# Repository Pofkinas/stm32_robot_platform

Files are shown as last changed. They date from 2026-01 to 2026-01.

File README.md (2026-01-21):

# STM32 Robot Platform

Modular robot platform for experimenting with basic robotics. Built around STM32F411RE (main controller) and ESP32 (encoder bridge + web interface).

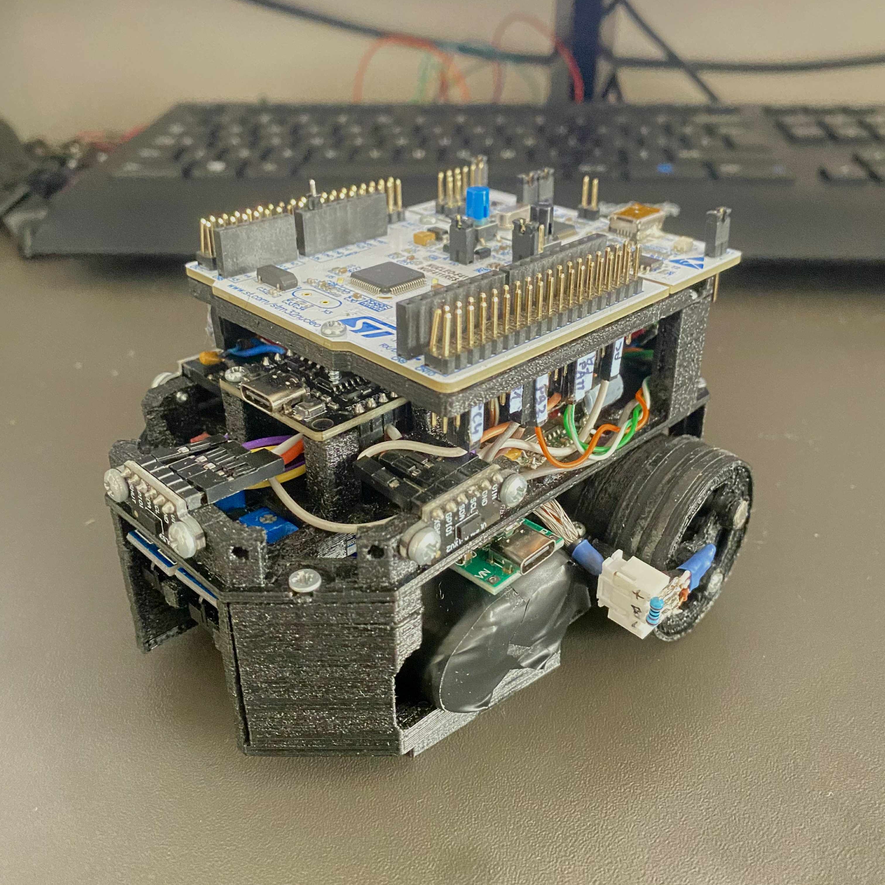
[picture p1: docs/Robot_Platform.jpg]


## Hardware

The platform uses 3D-printed chassis designed for modularity and easy prototyping. It is possible to configure sensor layer by suppressing/unsuppressing features. All parts are available as Fusion 360 files (`.f3z`) in the `hardware/` directory.

**Components:**

- STM32F411RE Nucleo board
- ESP32 DevKit
- TB6612FNG motor driver
- 2× 130 DC 3-6 V motors with custom 36:1 planetary gearboxes
- 3× VL53L0X time-of-flight sensors
- 2× DRV5032FCDBZR hall effect sensors for wheel encoders (see notes below)
- 2× TCRT5000 tracking sensors (not currently implemented)
- User button on PC0 (not currently implemented)
- MINI360 DC-DC step down buck converter (logic circuit)
- XL4015 DC-DC step down buck converter (power circuit)
- 18650 2S 15C Li-Ion battery pack

**Pinout:**

| **STM32 Pin** | **Function** |
|---|---|
| PA9, PA10 | UART TX/RX (ESP32 communication) |
| PB0, PB1 | Motor PWM (right, left) |
| PA4, PB2 | Motor A direction (IN1, IN2) |
| PA11, PA12 | Motor B direction (IN2, IN1) |
| PC1, PA6 | TCRT sensors (right, left) |
| PB8, PB9 | I2C1 SCL/SDA (VL53L0X) |
| PC4, PC5, PC2 | VL53L0X XSHUT (left, center, right) |
| PC0 | User button (reserved for future use) |

| **ESP32 Pin** | **Function** |
|---|---|
| D16, D17 | UART2 TX/RX (STM32 communication) |
| D4, D13 | Encoder interrupts (left, right) |

## Architecture

The firmware is structured around a mission-based task scheduler running as the main thread, periodically updating available tasks. Each mission consists of multiple tasks, with each task containing a sequence of actions that can be combined to create autonomous behaviors.

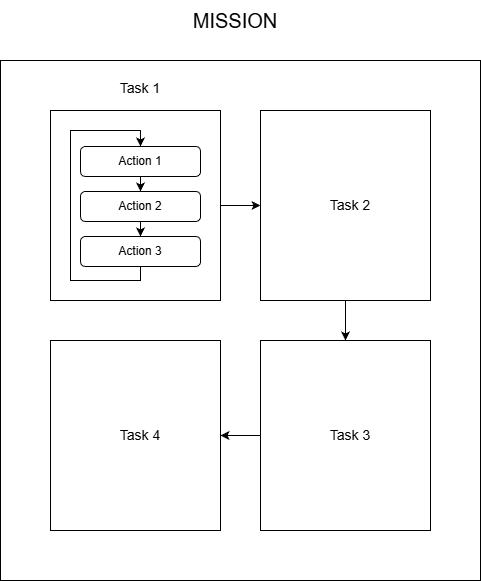
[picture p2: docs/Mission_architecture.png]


**Mission Architecture Flow:**
- Missions are queued in the scheduler and executed sequentially
- Each mission contains one or more tasks
- Tasks are broken down into actions (DriveDistance, Measure, WallFollow) that are serviced periodically
- Actions report completion status, allowing the scheduler to advance to the next step
- Failed actions trigger error handling and mission cancellation

**Available Actions:**
- `DriveDistance` — drives to set heading (degrees) for a specified distance (mm) at set speed (mm/s) using encoder feedback and odometry
- `Measure` — reads selected VL53L0X sensors
- `WallFollow` — follows a wall (left/right/center) at set speed (%) maintaining set offset distance using PID control

Missions are defined as semicolon-delimited strings sent via CLI or web interface. The mission scheduler executes actions sequentially.

**Communication Protocol:**

A custom binary protocol over UART between STM32 and ESP32 uses the following message structure:

```
[CMD_BYTE:1][ARG_COUNT:1][ARGS:n][\n]
```

- **CMD_BYTE**: 8-bit value containing command ID (7 bits) and direction bit (1 bit)
  - Bit 0: Direction (0=request, 1=response)
  - Bits 1-7: Command ID
- **ARG_COUNT**: Number of bytes in the arguments section
- **ARGS**: Raw argument data string (optional)
- **\n**: Message delimiter

## Control Panel Webpage

The web interface provides button-based command formation with two modes: instant send (commands execute immediately with field values) or manual construction via the custom command field (command buttons prefill this field). Mission builder allows creating multi-action sequences by adding tasks like "Measure" and "Wall Follow" with configurable parameters. All sent commands and debug messages from the STM32 are displayed in the real-time log panel. See `docs/Control_Panel.png`

## Software Architecture

```
stm32/                   # STM32 firmware
├── Application/
│   ├── Action/          # Action implementations
│   ├── Config/          # Hardware abstraction configs
│   ├── main.c
│   ├── mission_app.c    # Mission scheduler
│   ├── kinematics_app.c # Motor control, odometry
│   └── esp_comm_app.c   # ESP32 communication handler
├── Framework/           # PDF framework (submodule)
└── ThirdParty/          # STM32 HAL, FreeRTOS

esp32/                   # ESP32 firmware (PlatformIO)
├── src/                 # Main source
│   ├── main.cpp
│   ├── encoder.cpp      # Hall sensor interrupt handling
│   └── esp_protocol.cpp # UART protocol implementation
├── lib/                 # Web server, WiFi, logging
└── data/                # Web interface files (served via LittleFS)
```

**Dependencies:**
- STM32 firmware uses PDF (Platform Driver Framework) as a hardware abstraction layer, included as a git submodule from [github.com/Pofkinas/pdf](https://github.com/Pofkinas/pdf)
- ESP32 uses file system (LittleFS) to house web page, included as library dependency from [github.com/joltwallet/esp_littlefs](https://github.com/joltwallet/esp_littlefs.git#v1.20.3)

## Odometry & Kinematics

The `kinematics_app` tracks robot position and heading using differential drive equations. Encoder data from ESP32 (wheel RPM) is converted to linear and angular velocity, then integrated to estimate:
- X/Y position (mm) in global frame
- Heading angle (degrees)
- Velocity (mm/s)

## CLI Commands

The STM32 exposes a command-line interface via UART. Commands can be sent from a serial terminal or via the web interface. Alternatively, enable the CLI by defining `ENABLE_CLI` in `platform_config.h` and setting `DEBUG_UART` to `UART2` (ST-Link). Note that enabling CLI on the debug UART will disable debug message forwarding to the Robot Control Panel webpage.

See `stm32/Application/custom_cli_lut.c` for complete command list and syntax.

## VL53L0X Time-of-Flight Sensors

The robot uses three VL53L0X sensors operating in a custom high-speed, high-accuracy profile. On boot, the firmware performs automatic calibration (offset and crosstalk) to compensate for environmental conditions.

**Calibration Process:**
- Place robot in similar operating conditions with white calibration targets perpendicular to sensors at 100 mm distance
- Power on and wait for calibration to complete (~15 seconds)
- View calibration values printed in Robot Platform Control Panel

To disable the calibration process, set `.has_calib_data` to `true` in `stm32/Application/Config/vl53l0xv2_config.c` for each sensor and prefill calibration values from a previous calibration run (printed via debug UART).

## Build & Flash

When cloning/forking repo, init PDF submodules via:
```bash
git submodule update --init --recursive
```

**STM32:**
- Import `stm32/` as "Existing project" into Workspace in STM32CubeIDE
- Build and flash via ST-Link

**ESP32:**
- Install PlatformIO
- Navigate to `esp32/` and run `pio run -t upload`
- Upload filesystem: `pio run -t uploadfs`

**Web Interface:**
- Connect ESP32 to WiFi network (enter credentials in `esp32/include/config.h`)
- Using a serial console (baudrate 115200), reboot the ESP32 and watch logs for the hosted IP address
- Navigate to the ESP32's IP address in a browser

## PID Wall-Follow Tuning

The wall-follow action uses a PID controller to maintain a target distance from walls. Motor speed imbalance is partly offset by proportional value `MOTOR_x_SPEED_OFFSET` in `stm32\Application\Config\motor_config.h`.

**Quick tuning procedure:**
1. Start with Ki = 0, Kd = 0
2. Increase Kp until the robot oscillates, then reduce by 30-50%
3. Add Kd to dampen oscillation and reduce overshoot
4. Add minimal Ki to eliminate steady-state drift

## Known Issues

**Hall sensor choice:** The current hall sensors are practically unusable in encoder applications because of their low sampling rate of only 5 Hz. Consider upgrading to at least 1 kHz sampling rate **omnipolar non-latching** sensors. It is possible to embed magnets while printing in `Planet carrier middle`, removing the need for external encoder arm and fitting everything in a smaller footprint. Though for this case use sensors with at least 5 kHz (~12000 rpm / 6 (first stage gear ratio 6:1) × 3 magnets / 60) sampling rate.

**Wall-follow task:** Current implementation uses sensor data to calculate error for the PID controller, which directly adjusts motor speed (%). A better approach would be to control heading via the kinematics app. This primitive solution was a workaround for unreliable encoder sensors.

**ESP protocol:** Current implementation is overly complicated and confusing. Consider using dedicated bytes for actual commands instead of strings with byte count, plus adding error checking mechanisms (CRC, checksums).

**Motor RPM control:** Due to unusable encoders, motor RPM control and every component based on it (`motor_api` RPM control, `kinematics_app`, `drive_distance` action) remains poorly tested and may not function as intended.

**Motor calibration:** Motor imbalance is currently offset by proportional values (`MOTOR_A_SPEED_OFFSET` / `MOTOR_B_SPEED_OFFSET`). A polynomial calibration curve would be more accurate across the speed range.

## License

This project is licensed under the GNU General Public License v3.0. See the [LICENSE](LICENSE) file for more details

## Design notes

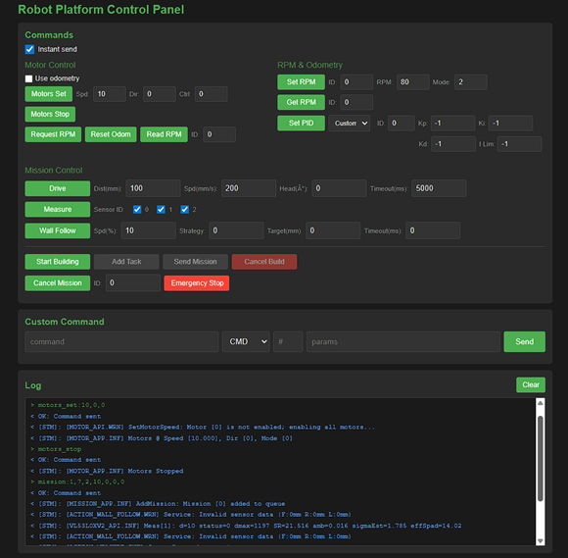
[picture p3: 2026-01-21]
docs/Control_Panel.png

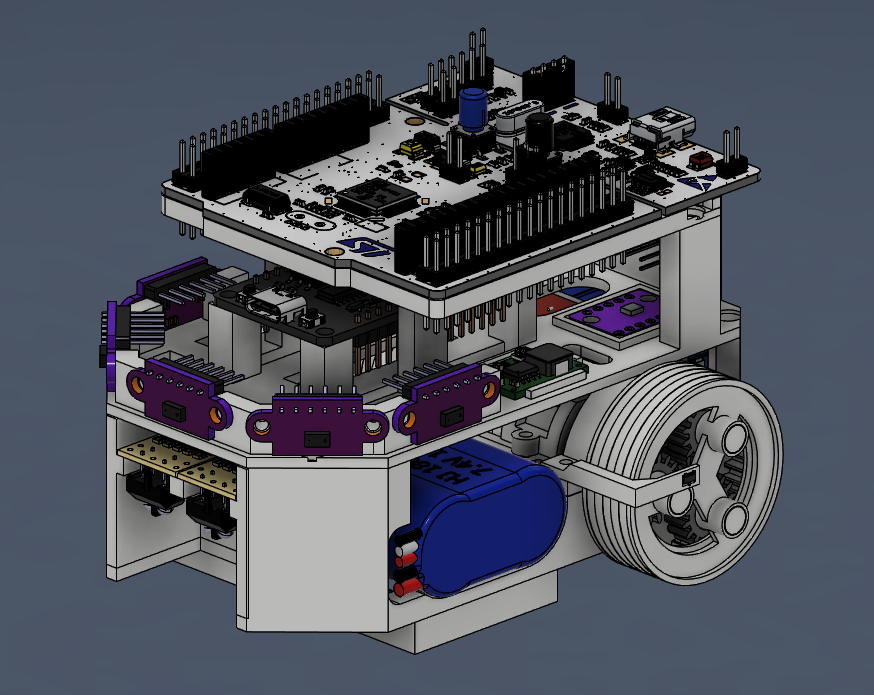
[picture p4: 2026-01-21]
docs/Robot_Platform_CAD.png

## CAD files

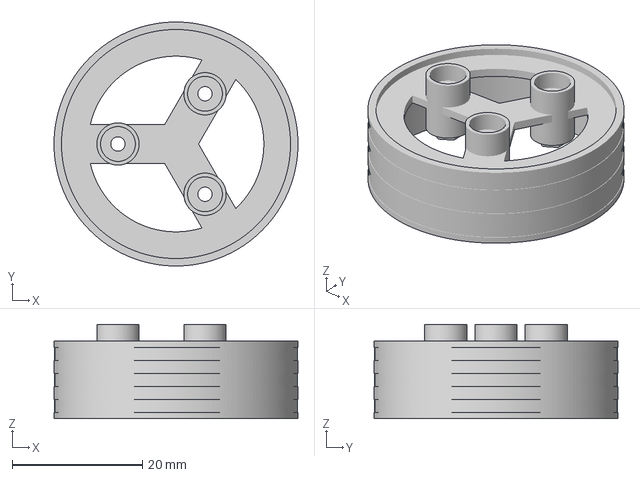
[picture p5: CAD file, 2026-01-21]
hardware/3d_print_parts/Gearbox/Wheel.3mf
37.5 x 37.5 x 14.5 mm

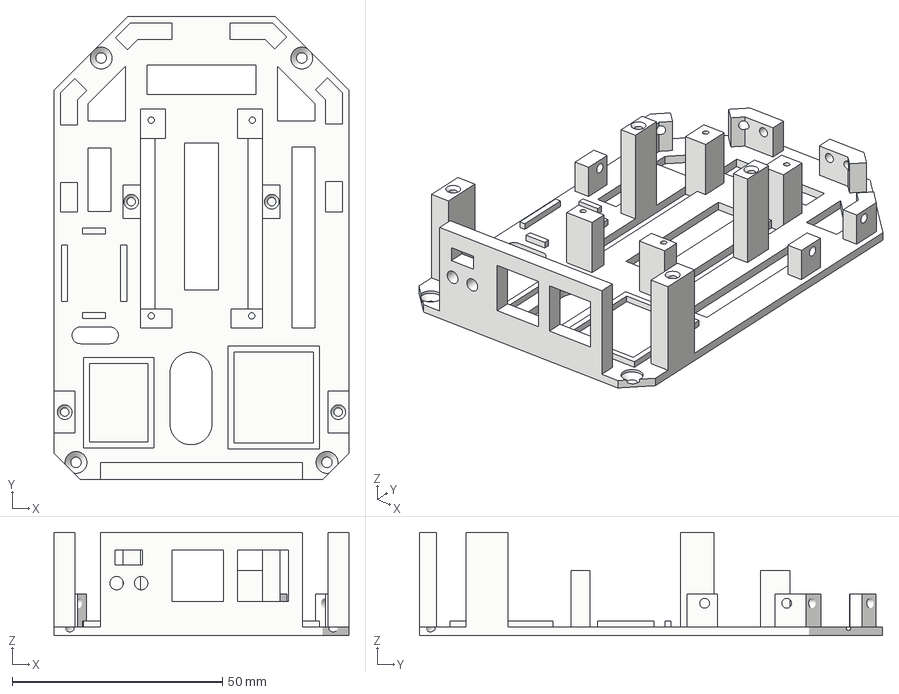
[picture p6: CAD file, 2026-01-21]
hardware/3d_print_parts/Sensor layer.3mf
70.0 x 110.0 x 24.5 mm

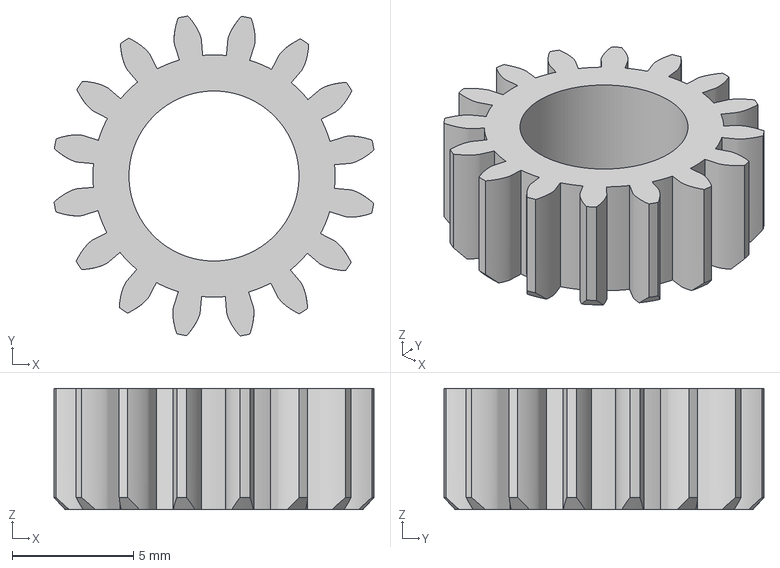
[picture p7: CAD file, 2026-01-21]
hardware/3d_print_parts/Gearbox/Planet gear 2nd stage (3x).3mf
13.2 x 13.2 x 5.00 mm

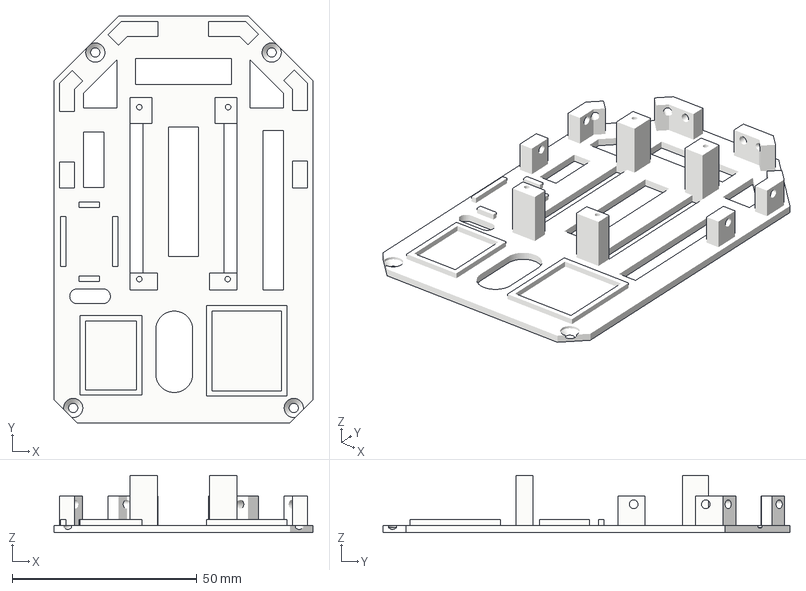
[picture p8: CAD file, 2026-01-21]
hardware/3d_print_parts/Sensor layer (no STM32 Nucleo).3mf
70.0 x 110.0 x 15.5 mm

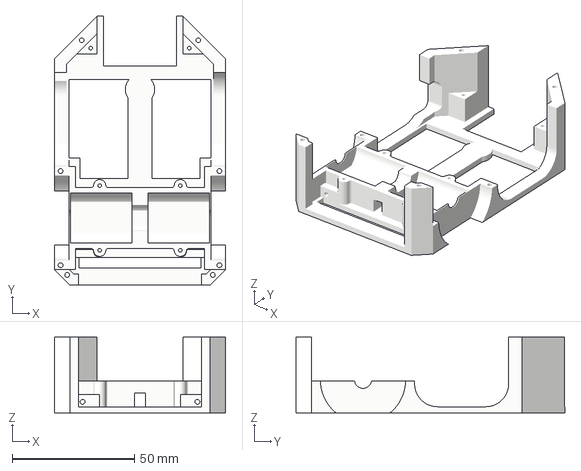
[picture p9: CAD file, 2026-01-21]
hardware/3d_print_parts/Chassis.3mf
70.0 x 110.0 x 31.0 mm

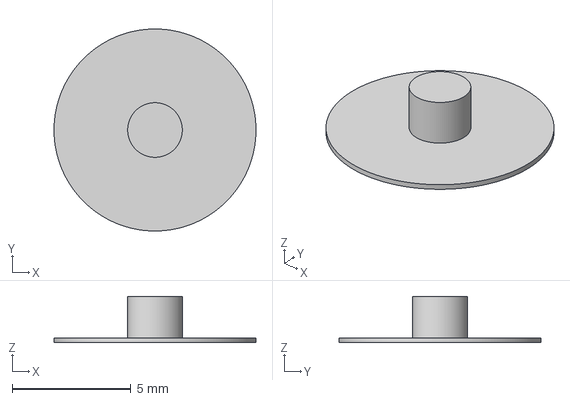
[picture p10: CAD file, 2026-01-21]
hardware/3d_print_parts/Gearbox/Pin (3x).3mf
8.50 x 8.50 x 1.95 mm

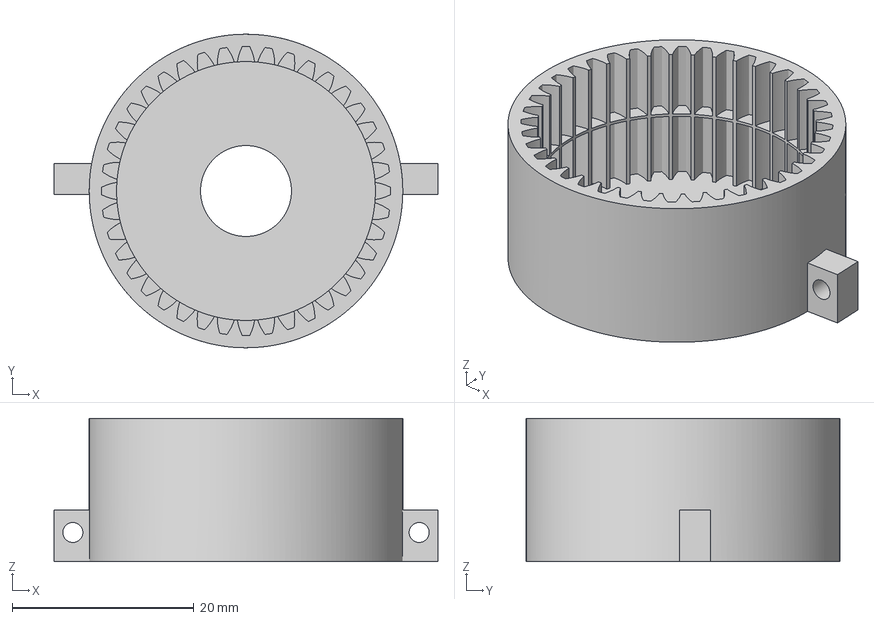
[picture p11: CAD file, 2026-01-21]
hardware/3d_print_parts/Gearbox/Ring gear body.3mf
42.2 x 34.5 x 15.8 mm

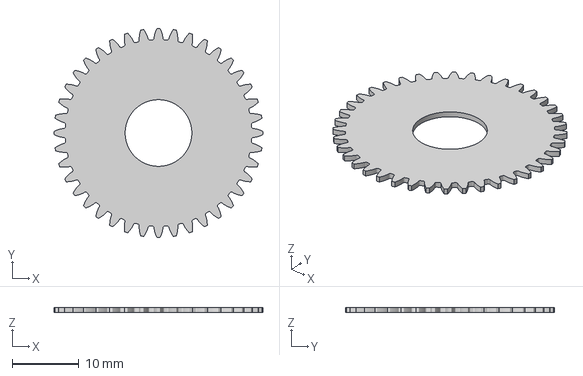
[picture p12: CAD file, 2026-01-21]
hardware/3d_print_parts/Gearbox/Ring gear partition.3mf
31.3 x 31.3 x 0.75 mm

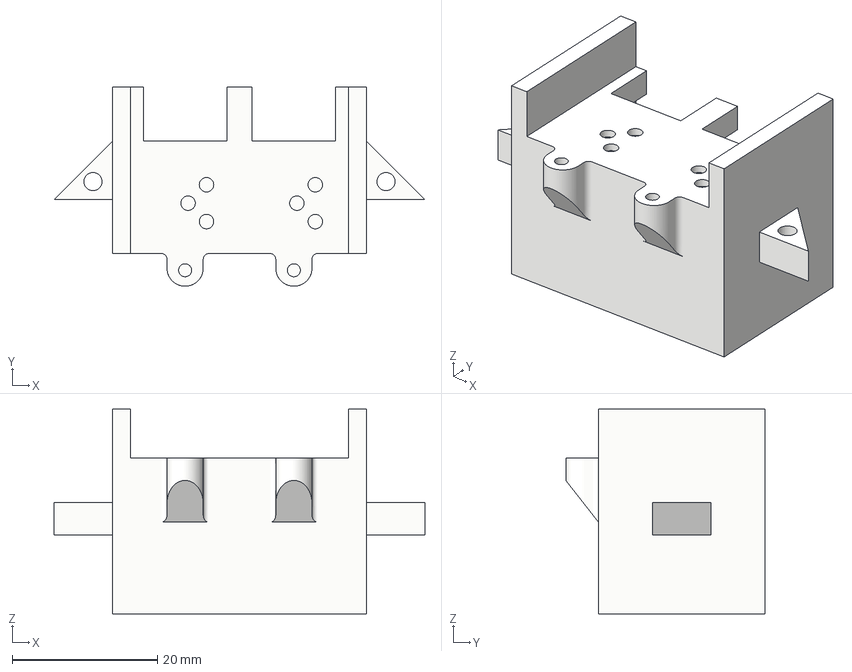
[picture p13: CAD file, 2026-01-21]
hardware/3d_print_parts/TCRT5000L double mount.3mf
51.2 x 27.5 x 28.2 mm

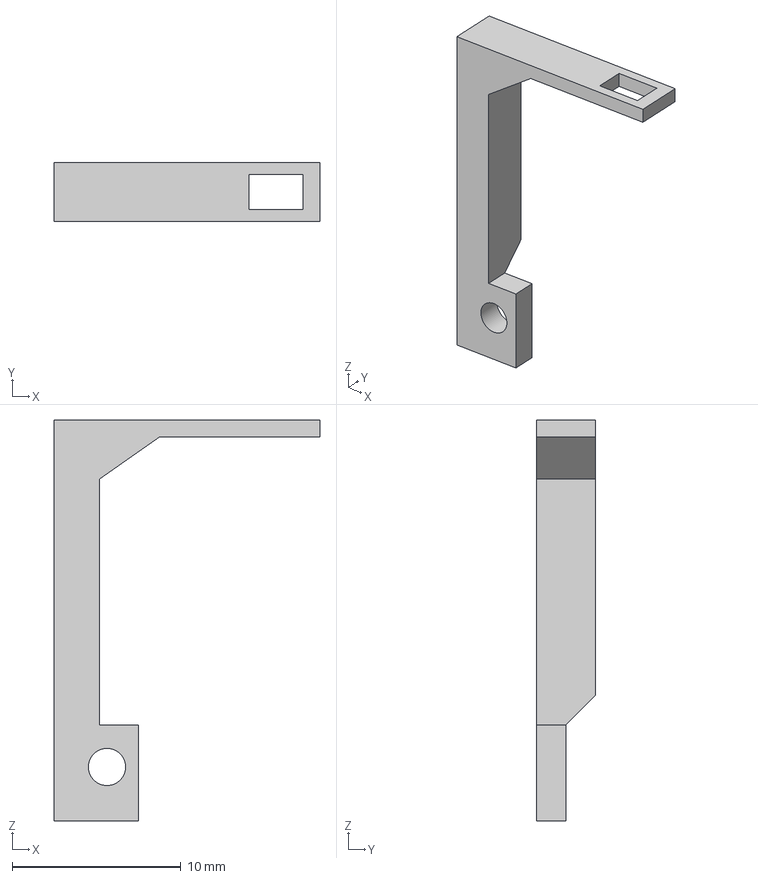
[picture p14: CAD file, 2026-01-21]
hardware/3d_print_parts/Gearbox/Encoder arm.3mf
15.8 x 3.50 x 23.8 mm

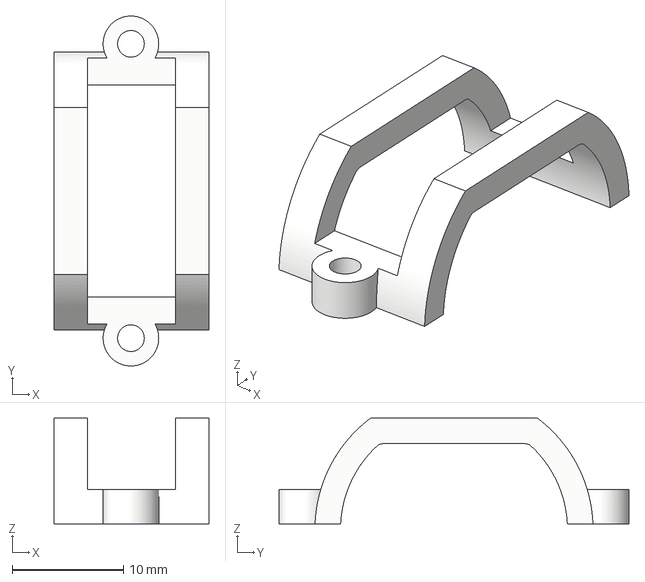
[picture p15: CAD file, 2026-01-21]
hardware/3d_print_parts/Motor mount top (2x).3mf
13.9 x 31.5 x 9.50 mm

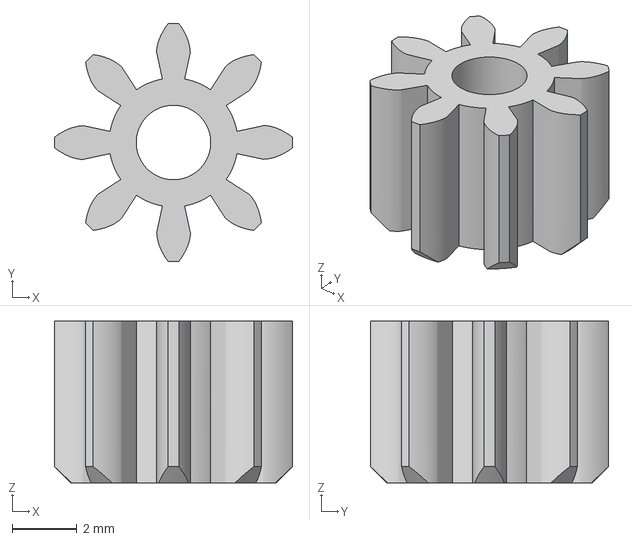
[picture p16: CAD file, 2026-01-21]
hardware/3d_print_parts/Gearbox/Input gear.3mf
7.35 x 7.35 x 5.00 mm

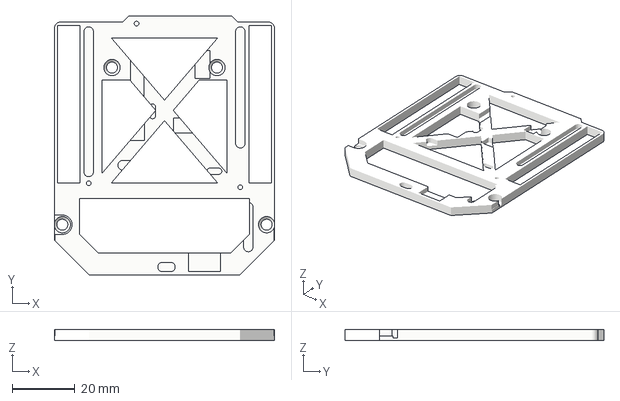
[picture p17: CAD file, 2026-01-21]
hardware/3d_print_parts/Nucleo mount.3mf
70.0 x 82.4 x 3.50 mm

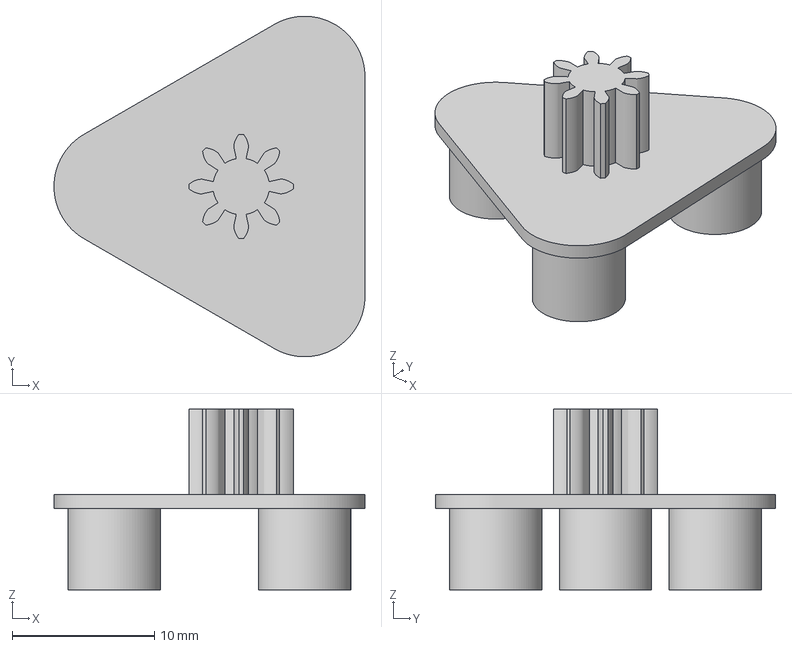
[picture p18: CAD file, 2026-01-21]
hardware/3d_print_parts/Gearbox/Planet carrier middle.3mf
21.9 x 23.9 x 12.7 mm

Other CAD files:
hardware/3d_print_parts/TCRT5000L mount.3mf
hardware/3d_print_parts/HW006 mount.3mf
hardware/3d_print_parts/Gearbox/Drive carrier pin (3x).3mf
hardware/3d_print_parts/Sensor layer (no ESP32).3mf
hardware/3d_print_parts/Brearing mount.3mf
hardware/3d_print_parts/Gearbox/2 Stage Planetary gearbox.f3z
hardware/3d_print_parts/Gearbox/Planet gear 1st stage (3x).3mf
hardware/3d_print_parts/Gearbox/Ring gear top.3mf
hardware/3d_print_parts/Stand.3mf

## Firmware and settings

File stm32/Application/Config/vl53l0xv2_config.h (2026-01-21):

#ifndef CONFIG_VL53L0XV2_CONFIG_H_
#define CONFIG_VL53L0XV2_CONFIG_H_
/**********************************************************************************************************************
 * Includes
 *********************************************************************************************************************/

#include "framework_config.h"

#include <stdbool.h>
#include <stdint.h>
#include "i2c_config.h"
#include "vl53l0x_api.h"
#include "gpio_config.h"

/**********************************************************************************************************************
 * Exported definitions and macros
 *********************************************************************************************************************/

#define VL53L0X_DEFAULT_ADDRESS 0x29

#define DEFAULT_STOP_TIMEOUT_MS 100
/// Calibration distances (mm)
#define DEFAULT_OFFSET_CALIB_DISTANCE_MM 100
#define DEFAULT_CROSSTALK_CALIB_DISTANCE_MM 200
#define FIX1616_FROM_INT(x) ((FixPoint1616_t)((uint32_t)(x) << 16))
#define FIX1616_FROM_FLOAT(x)  ((FixPoint1616_t)((float)(x) * 65536.0f + 0.5f))
#define FIX1616_TO_INT(x) ((int32_t)((x) >> 16))

#define MIN_DEFAULT_TIMEOUT 35 // Standard timing budget 30ms + overhead (max range: < 1.2 m (white target))
#define MIN_HIGH_ACCURACY_TIMEOUT 210 // Precise measurement timing budget 200ms + overhead (max range: < 1.2 m (white target))
#define MIN_LONG_RANGE_TIMEOUT 40 // Long range timing budget 33ms + overhead (max range: < 2 m (white target))
#define MIN_HIGH_SPEED_TIMEOUT 25 // High speed timing budget 20ms + overhead (max range: < 1.2 m (white target))

#define CUSTOM_RANGE_PROFILE_SIGNAL_RATE 0.1f
#define CUSTOM_RANGE_PROFILE_SIGMA 60
#define CUSTOM_RANGE_PROFILE_MEASUREMENT_TIME 25000

/**********************************************************************************************************************
 * Exported types
 *********************************************************************************************************************/

typedef enum eVl53l0x {
    eVl53l0x_First = 0,
    eVl53l0x_Front = eVl53l0x_First,
    eVl53l0x_Right,
    eVl53l0x_Left,
    eVl53l0x_Last
} eVl53l0x_t;

typedef enum eVl53l0xRangeProfile {
    eVl53l0xRangeProfile_First = 0,
    eVl53l0xRangeProfile_Default = eVl53l0xRangeProfile_First,
    eVl53l0xRangeProfile_HighAccuracy,
    eVl53l0xRangeProfile_LongRange,
    eVl53l0xRangeProfile_HighSpeed,
    eVl53l0xRangeProfile_Custom,
    eVl53l0xRangeProfile_Last
} eVl53l0xRangeProfile_t;

typedef enum eVl53l0xState {
    eVl53l0xState_First = 0,
    eVl53l0xState_Off = eVl53l0xState_First,
    eVl53l0xState_HwStandby,
    eVl53l0xState_Init,
    eVl53l0xState_SwStandby,
    eVl53l0xState_Measuring,
    eVl53l0xState_Last
} eVl53l0xState_t;

typedef struct sVl53l0xStaticDesc {
    eI2c_t i2c;
    uint8_t i2c_address;
    uint8_t crosstalk_compensation_en;
    FixPoint1616_t crosstalk_distance;
    VL53L0X_DeviceModes device_mode;
    bool has_xshut_pin;
    eGpio_t xshut_pin;
    eVl53l0xRangeProfile_t range_profile;
} sVl53l0xStaticDesc_t;

typedef struct sVl53l0xDynamicDesc {
    VL53L0X_Dev_t device;
    eVl53l0xState_t state;
    bool has_calib_data;
    uint32_t calib_SpadCount;
	uint8_t calib_isApertureSpads;
    uint8_t calib_VhvSettings;
	uint8_t calib_PhaseCal;
    int32_t offset;
    FixPoint1616_t crosstalk_value;
} sVl53l0xDynamicDesc_t;

/**********************************************************************************************************************
 * Exported variables
 *********************************************************************************************************************/

/**********************************************************************************************************************
 * Prototypes of exported functions
 *********************************************************************************************************************/

bool VL53L0XV2_Config_IsCorrectVl53l0x (const eVl53l0x_t vl53l0x_device);
const sVl53l0xStaticDesc_t *VL53L0XV2_Config_GetVl53l0xStaticDesc (const eVl53l0x_t vl53l0x_device);
const sVl53l0xDynamicDesc_t *VL53L0XV2_Config_GetVl53l0xDynamicDesc (const eVl53l0x_t vl53l0x_device);

#endif /* CONFIG_VL53L0XV2_CONFIG_H_ */

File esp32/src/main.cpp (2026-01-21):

#include <stdio.h>
#include <string.h>
#include "freertos/FreeRTOS.h"
#include "freertos/task.h"
#include "nvs_flash.h"

#include "uart.h"
#include "debug.h"
#include "encoder.h"
#include "esp_protocol.h"
#include "main.h"
#include "wifi.h"
#include "web_server.h"
#include "logger.h"
#include "config.h"

static Encoder encoders[eEncoderId_Last] = {
    Encoder(eEncoderId_RIGHT_1, ENCODER_RIGHT_PIN),
    Encoder(eEncoderId_LEFT_1, ENCODER_LEFT_PIN)
};

UART comm_uart(CMD_UART, CMD_UART_TX, CMD_UART_RX, CMD_BAUDRATE, CMD_BUFFER_SIZE, CMD_BUFFER_SIZE, ESP_MSG_DELIMITER);
WiFi wifi(WIFI_SSID, WIFI_PASSWORD);
WebServer web_server(WEB_SERVER_PORT);

char rx_buffer[CMD_BUFFER_SIZE];
sMessage_t rx_message = {.data = rx_buffer, .size = CMD_BUFFER_SIZE};

char response_buffer[CMD_RESPONSE_SIZE];
sMessage_t response_message = {.data = response_buffer, .size = CMD_RESPONSE_SIZE};

static void cmd_task(void *pvParameters);

bool web_command_handler(char* cmd, int type, sMessage_t params, sMessage_t *response) {
    if ((cmd == NULL) || (response == NULL)) {
        return false;
    }
    
    eEspCmd_t cmd_type = static_cast<eEspCmd_t>(type);
    
    DEBUG_INFO("Web command: cmd=%s type=%d params=%s\n", cmd, type, (params.data != NULL) ? params.data : "");
    
    // Build protocol command byte
    uint8_t protocol_cmd = ESP_MAKE_REQUEST(cmd_type);
    
    sMessage_t final_params = {.data = NULL, .size = params.size};
    char param_buffer[CMD_BUFFER_SIZE] = {0};

    switch (cmd_type) {
        case eEspCmd_CMD: {
            int written = 0;
            
            if (params.size > 0 && params.data[0] != '\0') {
                // If cmd already contains the ':' delimiter (e.g. "set_pid:"), don't add another one.
                if (strchr(cmd, ':') != NULL) {
                    written = snprintf(param_buffer, CMD_BUFFER_SIZE, "%s%s", cmd, params.data);
                } else {
                    written = snprintf(param_buffer, CMD_BUFFER_SIZE, "%s:%s", cmd, params.data);
                }
            } else {
                written = snprintf(param_buffer, CMD_BUFFER_SIZE, "%s", cmd);
            }
            
            if (written <= 0) {
                snprintf(response->data, response->size, "Failed to format command parameters");
                
                return false;
            }
            
            final_params.data = param_buffer;
        } break;
        case eEspCmd_RPM: {
            final_params = params;      
        } break;
        default: {
            snprintf(response->data, response->size, "Unknown command type: %d", type);
            
            return false;
        } break;
    }
        
    return comm_send(protocol_cmd, final_params, CMD_COMMS_TIMEOUT);
}

void logger_callback(const char* message) {
    web_server.add_log_message(message);
}

extern "C" void app_main() {
    // Initialize NVS (required for WiFi)
    esp_err_t ret = nvs_flash_init();
    if (ret == ESP_ERR_NVS_NO_FREE_PAGES || ret == ESP_ERR_NVS_NEW_VERSION_FOUND) {
        ESP_ERROR_CHECK(nvs_flash_erase());
        ret = nvs_flash_init();
    }
    ESP_ERROR_CHECK(ret);
    
    if (!Debug::init()) {
        return;
    }
    
    gpio_install_isr_service(0);
    
    if (!comm_uart.init()) {
        DEBUG_ERROR("Failed to init UART\n");
        
        return;
    }

    if (!comm_uart.flush()) {
        DEBUG_ERROR("Failed to flush UART\n");
        
        return;
    }

    for (eEncoderId_t encoder = eEncoderId_First; encoder < eEncoderId_Last; encoder = static_cast<eEncoderId_t>(encoder + 1)) {
        if (!encoders[encoder].init()) {
            DEBUG_ERROR("Failed to init encoder ID %d\n", encoder);
            
            return;
        }
    }

    if (!wifi.init()) {
        DEBUG_ERROR("Failed to init WiFi\n");
        
        return;
    }
    
    if (!wifi.connect()) {
        DEBUG_ERROR("Failed to connect to WiFi\n");
        
        return;
    }
    
    DEBUG_INFO("Connected to WiFi IP: %s\n", wifi.get_ip_address());
    
    // Initialize Logger with web server callback
    Logger::init();
    Logger::set_callback(logger_callback);
    
    if (!web_server.init()) {
        DEBUG_ERROR("Failed to init web server\n");
        return;
    }
    
    web_server.set_command_handler(web_command_handler);
    DEBUG_INFO("Web server started at http://%s:%d\n", wifi.get_ip_address(), WEB_SERVER_PORT);
    
    TaskHandle_t cmd_task_handle = NULL;

    xTaskCreate(cmd_task, "Cmd_task", CMD_STACK_SIZE, NULL, (tskIDLE_PRIORITY + 1), &cmd_task_handle);

    if (cmd_task_handle == NULL) {
        DEBUG_ERROR("Failed to create cmd_task\n");
        return;
    }
    
    DEBUG_INFO("Start OK\n");
    LOG_ESP("Start OK\n");

    vTaskDelete(NULL);
}

static void cmd_task(void *pvParameters) {
    while (1) {
        rx_message.size = CMD_BUFFER_SIZE;
        if (comm_uart.receive(&rx_message, portMAX_DELAY)) {
            if (rx_message.size != 0) {
                size_t len = rx_message.size;
                if (len >= CMD_BUFFER_SIZE) {
                    len = CMD_BUFFER_SIZE - 1;
                }

                rx_message.data[len] = '\0';
                
                while (len > 0 && (rx_message.data[len - 1] == '\n' || rx_message.data[len - 1] == '\r')) {
                    rx_message.data[len - 1] = '\0';
                    len--;
                }

                if (len > 0) {
                    DEBUG_INFO("Received: %s\n", rx_message.data);
                    LOG_STM("%s\n", rx_message.data);
                }

                if (!esp_protocol_parse(rx_message, &response_message)) {
                    // DEBUG_WARNING("%s", response_message.data);
                    // LOG_ESP("%s", response_message.data);
                }
            } else {
                // DEBUG_WARNING("Received empty message\n");
                // LOG_ESP("Received empty message\n");
            }

            memset(rx_message.data, 0, CMD_BUFFER_SIZE);
        }
    }
}

bool comm_send (const uint8_t command, const sMessage_t params, const uint32_t timeout) {
    static char buffer[CMD_BUFFER_SIZE] = {0};
    
    static sMessage_t output_command = {.data = buffer, .size = CMD_BUFFER_SIZE};
    memset(buffer, 0, CMD_BUFFER_SIZE);

    if (!esp_protocol_form_command(&output_command, command, params)) {
        return false;
    }

    DEBUG_INFO("Sent [%d bytes]: [0x%02X][0x%02X]%s", output_command.size, output_command.data[0], output_command.data[1], (output_command.size > 2) ? (char*)&output_command.data[2] : "");
    //LOG_ESP("Sent [%d bytes]: [0x%02X][0x%02X]%s", output_command.size, output_command.data[0], output_command.data[1], (output_command.size > 2) ? (char*)&output_command.data[2] : "");
    
    return comm_uart.transmit(output_command);
}

uint16_t get_encoder_rpm(const eEncoderId_t encoder) {
    if (encoder < eEncoderId_First || encoder >= eEncoderId_Last) {
        return false;
    }

    return encoders[encoder].getRPM();
}

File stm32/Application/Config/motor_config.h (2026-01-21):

#ifndef CONFIG_MOTOR_CONFIG_H_
#define CONFIG_MOTOR_CONFIG_H_
/**********************************************************************************************************************
 * Includes
 *********************************************************************************************************************/

#include "framework_config.h"

#include <stdbool.h>
#include "cmsis_os2.h"
#include "pwm_config.h"
#include "timer_config.h"

#ifdef USE_TB6612FNG
#include "gpio_config.h"
#endif /* USE_TB6612FNG */

#ifdef ENABLE_PID_CONTROL
#include "math_utils.h"
#endif /* ENABLE_PID_CONTROL */

/**********************************************************************************************************************
 * Exported definitions and macros
 *********************************************************************************************************************/

// TODO: There should be a polynomial function to calculate offset
#define MOTOR_A_SPEED_OFFSET 1.0f // Speed offset to compensate motor inequality
#define MOTOR_B_SPEED_OFFSET 1.07f

#define STOP_SPEED 0
#define MOTOR_DIRECTION_CHANGE_DELAY_MS 50U

#define INPUT_MIN_SPEED 0.0f
#define INPUT_MAX_SPEED 100.0f

/// Speed scaling limits (%)
#define MIN_SCALED_SPEED 18.0f
#define MAX_SCALED_SPEED 100.0f
#define SOFT_TURN_SPEED_OFFSET 10.0f

/// Ramp configuration
#define MOTOR_RAMP_STEPS 10
#define MOTOR_RAMP_SPEED_THRESHOLD 25
#define MOTOR_RAMP_TIMER_MS 2U
#define MOTOR_BRAKE_TIME_MS 10U

/// PWM Control configuration
#define CONTROL_PERIOD_MS 50U

#define MAX_RPM 400.0f
#define MIN_RPM 10.0f
#define MAX_PWM 255
#define BRAKE_RPM_THRESHOLD 5.0f
#define CHANGE_DIR_THRESHOLD 0.1 

/**********************************************************************************************************************
 * Exported types
 *********************************************************************************************************************/

typedef enum eMotor {
    eMotor_First = 0,
    eMotor_A = eMotor_First,
    eMotor_B,
    eMotor_Last
} eMotor_t;

typedef enum eMotorPosition {
    eMotorPosition_First = 0,
    eMotorPosition_Right = eMotorPosition_First,
    eMotorPosition_Left,
    eMotorPosition_Center,
    eMotorPosition_Last
} eMotorPosition_t;

typedef enum eMotorRotation {
    eMotorRotation_First = 0,
    eMotorRotation_CW = eMotorRotation_First,
    eMotorRotation_CCW,
    eMotorRotation_Stop,
    eMotorRotation_Brake,
    eMotorRotation_Last
} eMotorRotation_t;

typedef enum eMotorDirection {
    eMotorDirection_First = 0,
    eMotorDirection_Forward = eMotorDirection_First,
    eMotorDirection_Reverse,
    eMotorDirection_Right,
    eMotorDirection_RightSoft,
    eMotorDirection_Left,
    eMotorDirection_LeftSoft,
    eMotorDirection_Brake,
    eMotorDirection_BrakeLock,
    eMotorDirection_Stop,
    eMotorDirection_Last
} eMotorDirection_t;

typedef struct sMotorDriverDesc {
    eTimer_t timer;
    ePwm_t pwm_1;
    #ifdef USE_MX1508
    ePwm_t pwm_2;
    #endif /* USE_MX1508 */
    #ifdef USE_TB6612FNG
    eGpio_t in1;
    eGpio_t in2;
    #endif /* USE_TB6612FNG */
} sMotorDriverDesc_t;

typedef struct sMotor {
    osMutexAttr_t mutex_attributes;
    osTimerAttr_t timer_attributes;
    float motor_speed_offset;
    eMotorPosition_t position;
    eMotorRotation_t rotation[eMotorDirection_Last];
} sMotor_t;

/**********************************************************************************************************************
 * Exported variables
 *********************************************************************************************************************/

extern const osThreadAttr_t g_motor_thread_attributes;
extern const osMessageQueueAttr_t g_motor_message_queue_attributes;

/**********************************************************************************************************************
 * Prototypes of exported functions
 *********************************************************************************************************************/

bool Motor_Config_IsCorrectMotor (const eMotor_t motor);
bool Motor_Config_IsCorrectDirection (const eMotorDirection_t direction);
const sMotorDriverDesc_t *Motor_Config_GetMotorDriverDesc (const eMotor_t motor);
const sMotor_t *Motor_Config_GetMotorDesc (const eMotor_t motor);

#ifdef ENABLE_PID_CONTROL
const sPID_t *Motor_Config_GetMotorPIDParams (const eMotor_t motor);
#endif /* ENABLE_PID_CONTROL */

#endif /* CONFIG_MOTOR_CONFIG_H_ */

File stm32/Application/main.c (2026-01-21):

/**********************************************************************************************************************
 * Includes
 *********************************************************************************************************************/

#include "cmsis_os.h"
#include "FreeRTOSConfig.h"
#include "stm32f4xx_ll_rcc.h"
#include "stm32f4xx_ll_system.h"
#include "stm32f4xx_ll_utils.h"
#include "stm32f4xx_ll_pwr.h"
#include "stm32f4xx_ll_usart.h"
#include "usart.h"
#include "cli_app.h"
#include "led_app.h"
#include "motor_app.h"
#include "debug_api.h"
#include "heap_api.h"
#include "timer_driver.h"
#include "baudrate.h"

#include "mission_app.h"

/**********************************************************************************************************************
 * Private definitions and macros
 *********************************************************************************************************************/

/**********************************************************************************************************************
 * Private typedef
 *********************************************************************************************************************/

/**********************************************************************************************************************
 * Private constants
 *********************************************************************************************************************/

#ifdef DEBUG_MAIN
CREATE_MODULE_NAME (MAIN)
#else
CREATE_MODULE_NAME_EMPTY
#endif /* DEBUG_MAIN */

static const osThreadAttr_t g_init_thread_attributes = {
    .name = "Main_Init",
    .stack_size = (256 * 8),
    .priority = osPriorityRealtime
};

/**********************************************************************************************************************
 * Private variables
 *********************************************************************************************************************/

volatile unsigned long ulHighFrequencyTimerTicks;

static osThreadId_t g_init_thread = NULL;

/**********************************************************************************************************************
 * Exported variables and references
 *********************************************************************************************************************/

/**********************************************************************************************************************
 * Prototypes of private functions
 *********************************************************************************************************************/

static void SystemClock_Config (void);
void configureTimerForRunTimeStats (void);
void TIM1_UP_TIM10_IRQHandler (void);
unsigned long getRunTimeCounterValue (void);

static void Main_Init_Thread (void *arg);

/**********************************************************************************************************************
 * Definitions of private functions
 *********************************************************************************************************************/

static void SystemClock_Config (void) {
    LL_FLASH_SetLatency(LL_FLASH_LATENCY_3);
    while(LL_FLASH_GetLatency()!= LL_FLASH_LATENCY_3) {}
    LL_PWR_SetRegulVoltageScaling(LL_PWR_REGU_VOLTAGE_SCALE1);
    LL_RCC_HSI_SetCalibTrimming(16);
    LL_RCC_HSI_Enable();

    while(LL_RCC_HSI_IsReady() != 1) {}
    LL_RCC_PLL_ConfigDomain_SYS(LL_RCC_PLLSOURCE_HSI, LL_RCC_PLLM_DIV_8, 100, LL_RCC_PLLP_DIV_2);
    LL_RCC_PLL_Enable();

    while(LL_RCC_PLL_IsReady() != 1) {}
    while (LL_PWR_IsActiveFlag_VOS() == 0) {}
    LL_RCC_SetAHBPrescaler(LL_RCC_SYSCLK_DIV_1);
    LL_RCC_SetAPB1Prescaler(LL_RCC_APB1_DIV_2);
    LL_RCC_SetAPB2Prescaler(LL_RCC_APB2_DIV_1);
    LL_RCC_SetSysClkSource(LL_RCC_SYS_CLKSOURCE_PLL);

    while(LL_RCC_GetSysClkSource() != LL_RCC_SYS_CLKSOURCE_STATUS_PLL) {}
    LL_SetSystemCoreClock(SYSTEM_CLOCK_HZ);

    if (HAL_InitTick (TICK_INT_PRIORITY) != HAL_OK) {
        __disable_irq();
        while (1) {}
    }
}

void configureTimerForRunTimeStats (void) {
    ulHighFrequencyTimerTicks = 0;
    LL_TIM_EnableIT_UPDATE(TIM10);
    LL_TIM_EnableCounter(TIM10);
}

unsigned long getRunTimeCounterValue (void) {
    return ulHighFrequencyTimerTicks;
}

void TIM1_UP_TIM10_IRQHandler (void) {
    if (LL_TIM_IsActiveFlag_UPDATE(TIM10)) {
        ulHighFrequencyTimerTicks++;
        LL_TIM_ClearFlag_UPDATE(TIM10);
    }
}

// Workaround for VL53L0X Init that requires Kernel to be running
static void Main_Init_Thread (void *arg) {
    bool init_success = true;

    Timer_Driver_InitAllTimers();
    Timer_Driver_Start(eTimer_TIM10);

    // if (!CLI_APP_Init(UART_2_BAUDRATE)) {
    //     init_success = false;
    // }

    if (!Heap_API_Init()) {
        while (1) {}
    }

    if (!Debug_API_Init(UART_1_BAUDRATE)) {
        while (1) {}
    }

    if (!LED_APP_Init()) {
        TRACE_ERR("LED_APP_Init failed\n");

        init_success = false;
    }

    if (!Motor_APP_Init()) {
        TRACE_ERR("Motor_APP_Init failed\n");

        init_success = false;
    }

    if (!Mission_APP_Init()) {
        TRACE_ERR("Mission_APP_Init failed\n");

        init_success = false;
    }

    if (!init_success) {
        while (1) {}
    }

    TRACE_INFO("Start OK\n");

    osThreadTerminate(g_init_thread);
}

/**********************************************************************************************************************
 * Definitions of exported functions
 *********************************************************************************************************************/

int main (void) {
    LL_APB2_GRP1_EnableClock(LL_APB2_GRP1_PERIPH_SYSCFG);
    LL_APB1_GRP1_EnableClock(LL_APB1_GRP1_PERIPH_PWR);

    NVIC_SetPriorityGrouping(NVIC_PRIORITYGROUP_4);

    NVIC_SetPriority(PendSV_IRQn, NVIC_EncodePriority(NVIC_GetPriorityGrouping(), 15, 0));
    NVIC_SetPriority(SysTick_IRQn, NVIC_EncodePriority(NVIC_GetPriorityGrouping(), 15, 0));

    SystemClock_Config();

    osKernelInitialize();

    g_init_thread = osThreadNew(Main_Init_Thread, NULL, &g_init_thread_attributes);

    if (g_init_thread == NULL) {
        while (1) {}
    }

    osKernelStart();

    while (1) {}
}

void HAL_TIM_PeriodElapsedCallback(TIM_HandleTypeDef *htim) {
    if (htim->Instance == TIM2) {
        HAL_IncTick();
    }
}

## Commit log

2026-01-21 feat(hardware): add hardware
    [2 Stage Planetary gearbox.f3z, Brearing mount.3mf, Chassis.3mf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]
2026-01-21 feat(stm32): add PDF framework
2026-01-21 feat(stm32): add ThirdParty drivers
2026-01-21 feat(stm32): add CubeIDE project
2026-01-21 feat(stm32/thirdparty/FreeRTIOSConfig): enable FPU and increase heap
2026-01-21 feat(esp32): add encoder and web server firmware
    [partitions.csv]
2026-01-21 feat(stm32/config): add project configuration
2026-01-21 feat(stm32/kinematics): add kinematics
2026-01-21 feat(stm32/mission): add mission scheduler
2026-01-21 feat(stm32/action): add action state
2026-01-21 feat(stm32/action_drive_distance): add drive distance action
2026-01-21 feat(stm32/action_measure): add measure action
2026-01-21 feat(stm32/action_wall_fallow): add wall fallow action
2026-01-21 feat(stm32/cli): add custom cli commands
2026-01-21 feat(stm32/esp_protocol): add esp32 custom comm protocol
2026-01-21 feat(stm32/main): add main
